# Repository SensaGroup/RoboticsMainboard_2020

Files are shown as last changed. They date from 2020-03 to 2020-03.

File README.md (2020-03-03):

# SENSA - Robotics_Mainboard

SENSA Mainboard is used on the Eurobot 2020 competition.

## Description
The Mainboard is the commander of the robot system. 
We used an Arduino Mega for the base and we developed the extension board

## Features
- 5V/5VA/12V inputs with protection
- 2 Sockets for stepper drivers, based on the A4988 pinout
- 6x servo pinouts with external 5V power supply
- 6x 12V pneumatic valve controller
- 5x 1AMP relays 
- AX-12 support
- 6x optoisolated 12V infrared sensor inputs
- 6x binary 5V sensor inputs
- NRF24L01
- I2C/UART pinouts

## Software
All software is written in C for AVR.
View README in the Software folder.

## Pictures
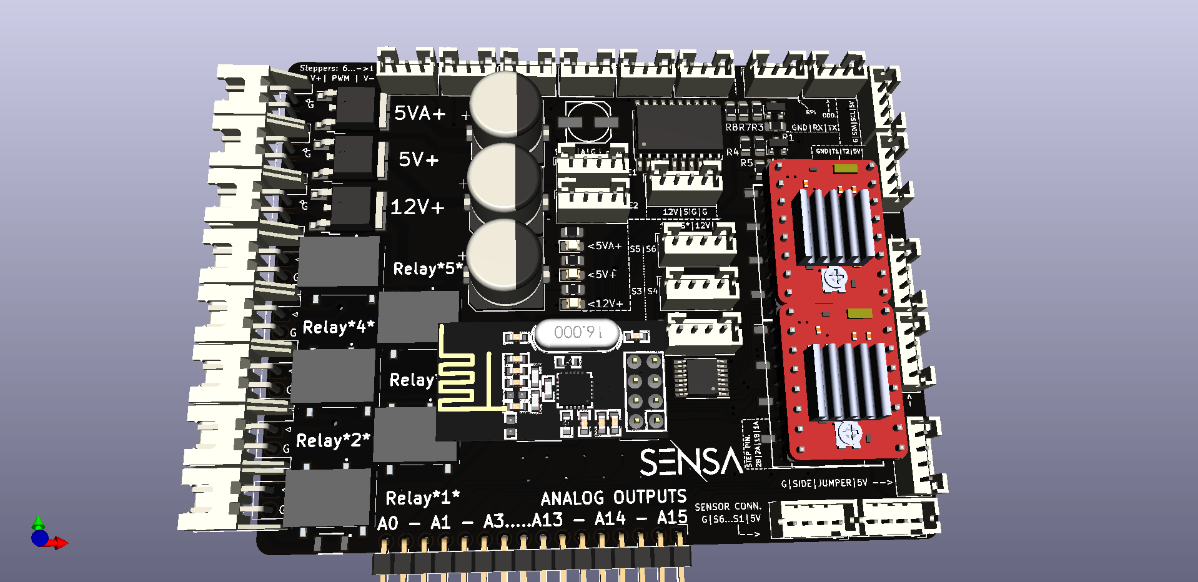
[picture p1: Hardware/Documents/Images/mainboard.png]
Top_view


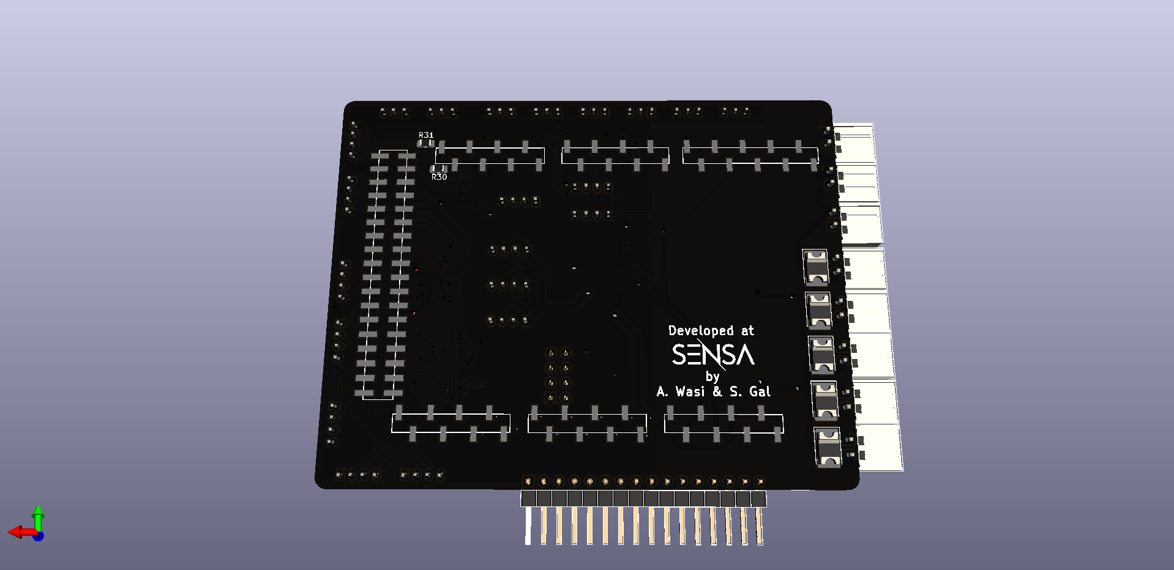
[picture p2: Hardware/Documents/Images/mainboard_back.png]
Back_view


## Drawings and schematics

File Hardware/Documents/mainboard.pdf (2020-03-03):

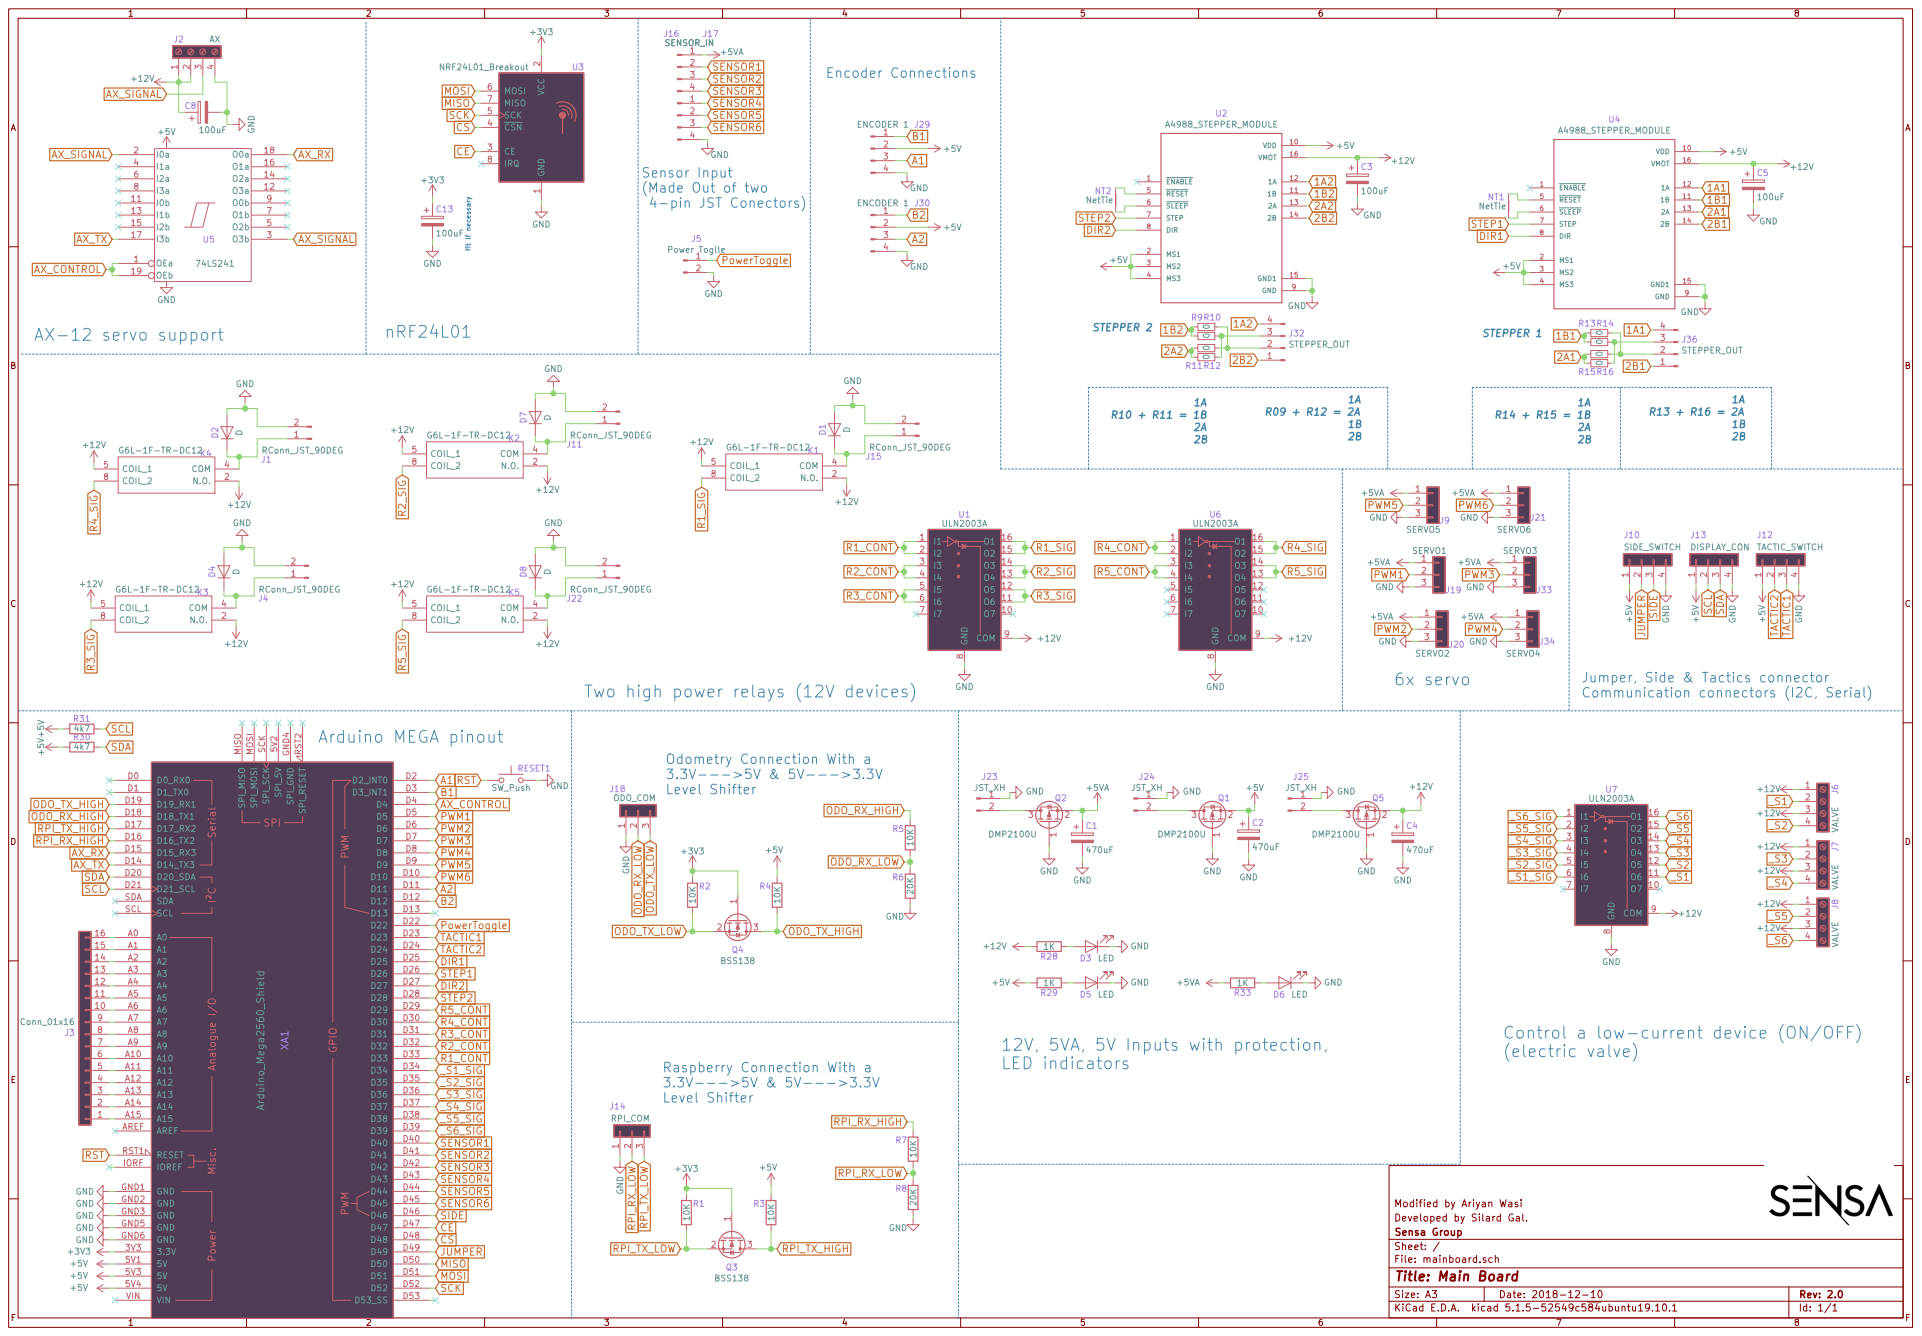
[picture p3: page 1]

2 CE 3 CSN 4 SCK 5 MOSI 6 MISO 7

2B Sensor Input
(Made Out of two
4-pin JST Conectors)

6x servo Two high power relays (12V devices)

Jumper, Side & Tactics connector
Communication connectors (I2C, Serial)

Control a low-current device (ON/OFF)
(electric valve)

Modified by Ariyan Wasi
Developed by Silard Gal.
File: mainboard.sch Sheet: / Sensa Group

Id: 1/1 Title: Main Board

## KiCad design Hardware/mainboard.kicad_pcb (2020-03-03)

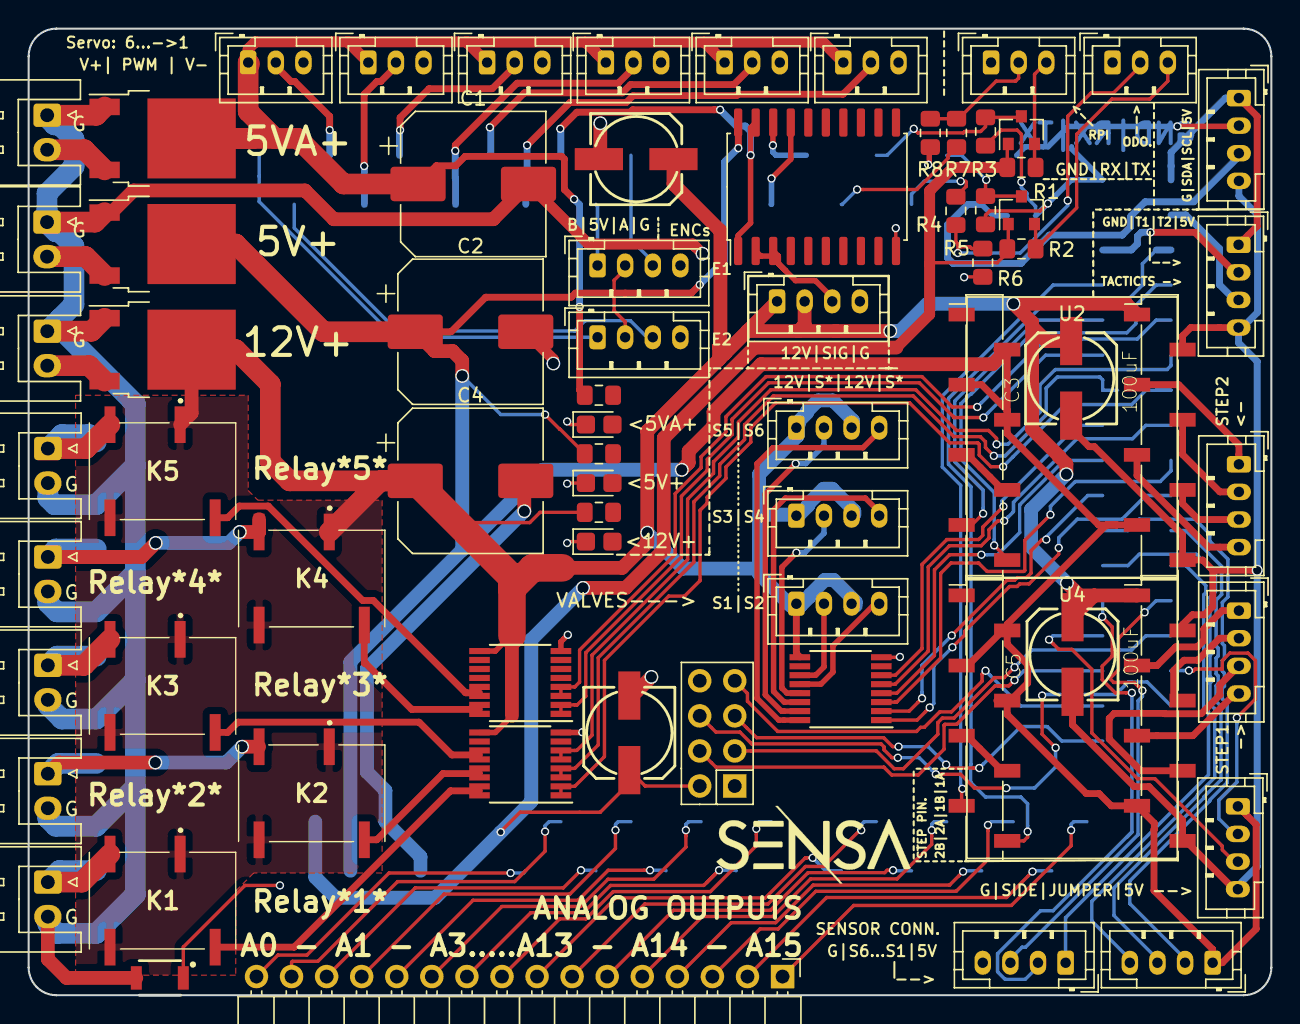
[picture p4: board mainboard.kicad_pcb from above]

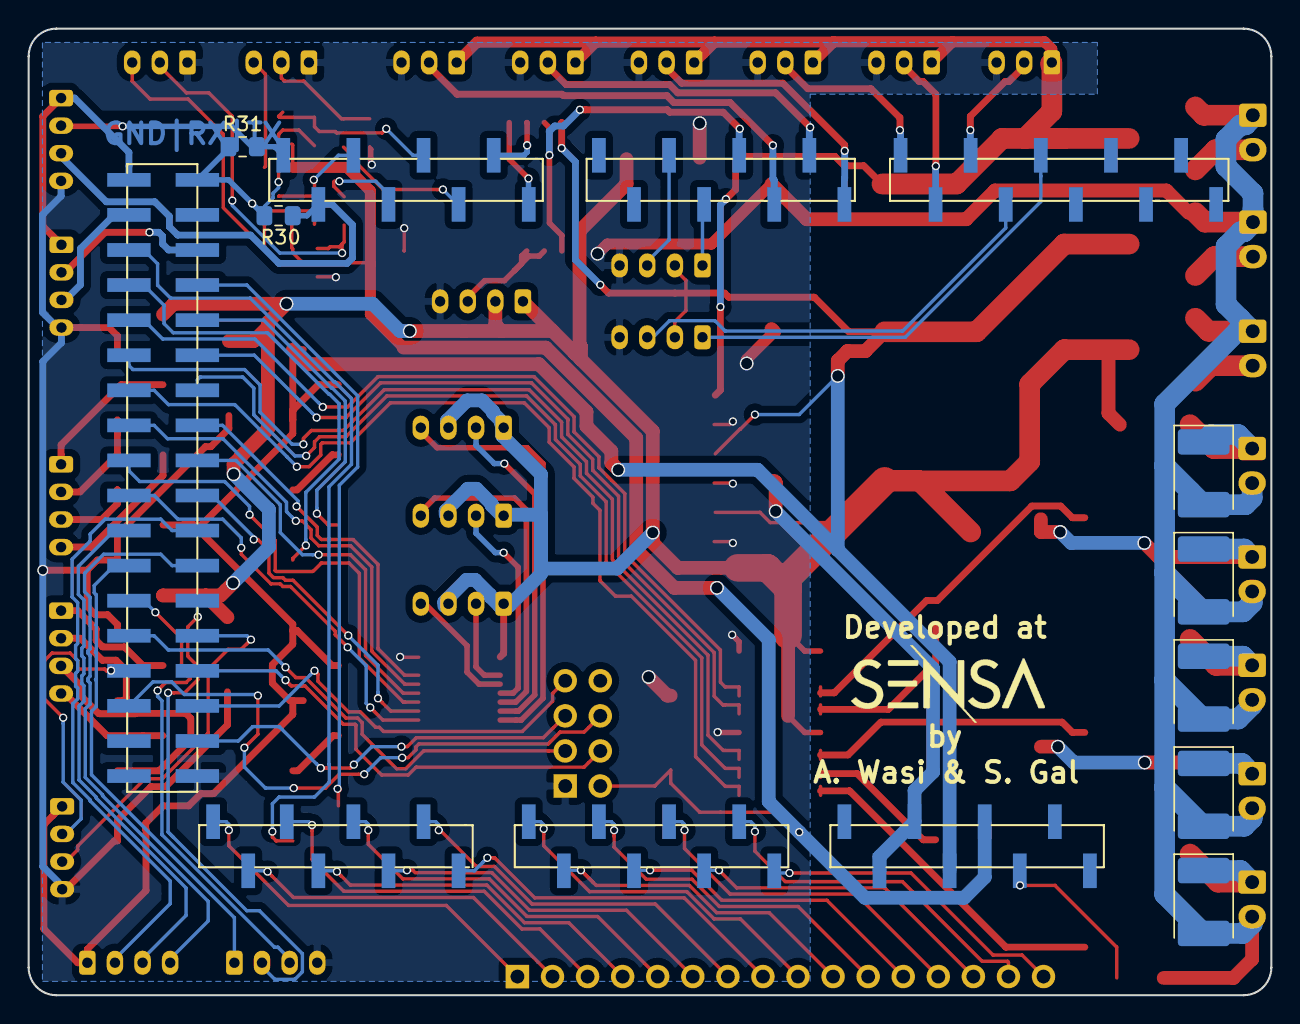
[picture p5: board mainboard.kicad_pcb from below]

Board: 2 copper layers, 90.0 x 70.0 mm, 79 parts (7 on the bottom side), 110 nets.

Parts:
5V+, 5VA+, 12V+: JST_XH; JST_XH_S2B-XH-A_1x02_P2.50mm_Horizontal
12V|S*|12V|S*: VALVE; JST_PH_B4B-PH-K_1x04_P2.00mm_Vertical
B|5V|A|G: ENCODER 1; JST_PH_B4B-PH-K_1x04_P2.00mm_Vertical
C1, C2, C4: 470uF; CP_Elec_10x10
C3, C5, C8, C13: 100uF; CAPAE0607X600N
D1, D2, D4, D7, D8: D; D_2114_3652Metric_Pad1.85x3.75mm_HandSolder
D3, D5, D6: LED; LED_0805_2012Metric_Castellated
G: RConn_JST_90DEG; JST_XH_S2B-XH-A_1x02_P2.50mm_Horizontal
G#2, G#3, G#4, G#5: RConn_JST_90DEG; JST_XH_S2B-XH-A_1x02_P2.50mm_Horizontal
J2: AX; JST_PH_B4B-PH-K_1x04_P2.00mm_Vertical
J3: Conn_01x16; PinHeader_1x16_P2.54mm_Horizontal
J7: VALVE; JST_PH_B4B-PH-K_1x04_P2.00mm_Vertical
J9: SERVO5; JST_PH_B3B-PH-K_1x03_P2.00mm_Vertical
J10: SIDE_SWITCH; JST_PH_B4B-PH-K_1x04_P2.00mm_Vertical
J12: TACTIC_SWITCH; JST_PH_B4B-PH-K_1x04_P2.00mm_Vertical
J13: DISPLAY_CON; JST_PH_B4B-PH-K_1x04_P2.00mm_Vertical
J14: RPI_COM; JST_PH_B3B-PH-K_1x03_P2.00mm_Vertical
J16, J17: SENSOR_IN; JST_PH_B4B-PH-K_1x04_P2.00mm_Vertical
J18: ODO_COM; JST_PH_B3B-PH-K_1x03_P2.00mm_Vertical
J19: SERVO1; JST_PH_B3B-PH-K_1x03_P2.00mm_Vertical
J20: SERVO2; JST_PH_B3B-PH-K_1x03_P2.00mm_Vertical
J21: SERVO6; JST_PH_B3B-PH-K_1x03_P2.00mm_Vertical
J30: ENCODER 1; JST_PH_B4B-PH-K_1x04_P2.00mm_Vertical
J32, J36: STEPPER_OUT; JST_PH_B4B-PH-K_1x04_P2.00mm_Vertical
J33: SERVO3; JST_PH_B3B-PH-K_1x03_P2.00mm_Vertical
J34: SERVO4; JST_PH_B3B-PH-K_1x03_P2.00mm_Vertical
K1, K2, K3, K4, K5: G6L-1F-TR-DC12; G6L1FTRDC5
NT1, NT2: NetTie; NetTie-2_SMD_Pad0.5mm
Q1, Q2, Q5: DMP2100U; TO-252-2
Q3, Q4: BSS138; SOT-23
R1, R2, R3, R4, R5, R7: 10K; R_0805_2012Metric_Pad1.15x1.40mm_HandSolder
R6, R8: 20K; R_0805_2012Metric_Pad1.15x1.40mm_HandSolder
R28, R29, R33: 1K; R_0805_2012Metric_Pad1.15x1.40mm_HandSolder
R30, R31: 4k7; R_0805_2012Metric_Pad1.15x1.40mm_HandSolder
RESET1: SW_Push; B3U-1000P
S1,S2: VALVE; JST_PH_B4B-PH-K_1x04_P2.00mm_Vertical
U1, U6, U7: ULN2003A; TSSOP-16_4.4x5mm_P0.65mm
U2, U4: A4988_STEPPER_MODULE; STEP_SMD
U3: NRF24L01_Breakout; PinSocket_2x04_P2.54mm_Vertical
U5: 74LS241; SOIC-20W_7.5x12.8mm_P1.27mm
XA1: Arduino_Mega2560_Shield

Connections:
1A1: J36.4, U4.12
1A2: J32.4, U2.12
1B1: J36.3, U4.11
1B2: J32.3, U2.11
2A1: J36.2, U4.13
2A2: J32.2, U2.13
2B1: J36.1, U4.14
2B2: J32.1, U2.14
+3V3: C13.+, Q3.1, Q4.1, R1.1, R2.1, U3.2, XA1.3V3
+5V: B|5V|A|G.2, C2.1, J10.1, J12.1, J13.1, J30.2, Q1.2, R3.1, R4.1, R29.2, R30.1, R31.1, U2.2, U2.3, U2.4, U2.10, U4.2, U4.3, U4.4, U4.10, U5.20, XA1.5V1, XA1.5V3, XA1.5V4
+5VA: C1.1, J9.1, J16.1, J19.1, J20.1, J21.1, J33.1, J34.1, Q2.2, R33.2
+12V: 12V|S*|12V|S*.1, 12V|S*|12V|S*.3, C3.+, C4.1, C5.+, C8.+, J2.1, J2.2, J7.1, J7.3, K1.2, K1.5, K2.2, K2.5, K3.2, K3.5, K4.2, K4.5, K5.2, K5.5, Q5.2, R28.2, S1,S2.1, S1,S2.3, U1.9, U2.16, U4.16, U6.9, U7.9
A1: B|5V|A|G.3, XA1.D2
A2: J30.3, XA1.D11
AX_CONTROL: U5.1, U5.19, XA1.D4
AX_RX: U5.18, XA1.D15
AX_SIGNAL: J2.3, U5.2, U5.3
AX_TX: U5.17, XA1.D14
B1: B|5V|A|G.1, XA1.D3
B2: J30.1, XA1.D12
CE: U3.3, XA1.D47
CS: U3.4, XA1.D48
DIR1: U4.8, XA1.D25
DIR2: U2.8, XA1.D27
GND: 5V+.1, 5VA+.1, 12V+.1, B|5V|A|G.4, C1.2, C2.2, C3.-, C4.2, C5.-, C8.-, C13.-, D1.2, D2.2, D3.1, D4.2, D5.1, D6.1, D7.2, D8.2, G.2, G#2.2, G#3.2, G#4.2, G#5.2, J2.4, J9.3, J10.4, J12.4, J13.4, J14.1, J17.4, J18.1, J19.3, J20.3, J21.3, J30.4, J33.3, J34.3, Q1.1, Q2.1, Q5.1, R6.2, R8.2, RESET1.2, U1.8, U2.9, U2.15, U3.1, U4.9, U4.15, U5.10, U6.8, U7.8, XA1.GND1, XA1.GND2, XA1.GND3, XA1.GND5, XA1.GND6
JUMPER: J10.2, XA1.D49
MISO: U3.7, XA1.D50
MOSI: U3.6, XA1.D51
unnamed: D1.1, G#4.1, K1.4
unnamed: D2.1, G.1, K4.4
unnamed: D3.2, R28.1
unnamed: D4.1, G#2.1, K3.4
unnamed: D5.2, R29.1
unnamed: D6.2, R33.1
unnamed: D7.1, G#3.1, K2.4
unnamed: D8.1, G#5.1, K5.4
unnamed: J3.1, XA1.A15
unnamed: J3.2, XA1.A14
unnamed: J3.3, XA1.A13
unnamed: J3.4, XA1.A12
unnamed: J3.5, XA1.A11
unnamed: J3.6, XA1.A10
unnamed: J3.7, XA1.A9
unnamed: J3.8, XA1.A8
unnamed: J3.9, XA1.A7
unnamed: J3.10, XA1.A6
unnamed: J3.11, XA1.A5
unnamed: J3.12, XA1.A4
unnamed: J3.13, XA1.A3
unnamed: J3.14, XA1.A2
unnamed: J3.15, XA1.A1
unnamed: J3.16, XA1.A0
unnamed: 5VA+.2, Q2.3
unnamed: 5V+.2, Q1.3
unnamed: 12V+.2, Q5.3
unnamed: NT1.1, U4.5
unnamed: NT1.2, U4.6
unnamed: NT2.1, U2.5
unnamed: NT2.2, U2.6
ODO_RX_HIGH: R5.1, XA1.D18
ODO_RX_LOW: J18.2, R5.2, R6.1
ODO_TX_HIGH: Q4.3, R4.2, XA1.D19
ODO_TX_LOW: J18.3, Q4.2, R2.2
PWM1: J19.2, XA1.D5
PWM2: J20.2, XA1.D6
PWM3: J33.2, XA1.D7
PWM4: J34.2, XA1.D8
PWM5: J9.2, XA1.D9
PWM6: J21.2, XA1.D10
R1_CONT: U1.1, U1.2, XA1.D33
R1_SIG: K1.8, U1.15, U1.16
R2_CONT: U1.3, U1.4, XA1.D32
R2_SIG: K2.8, U1.13, U1.14
R3_CONT: U1.5, U1.6, XA1.D31
R3_SIG: K3.8, U1.11, U1.12
R4_CONT: U6.1, U6.2, XA1.D30
R4_SIG: K4.8, U6.15, U6.16
R5_CONT: U6.3, U6.4, XA1.D29
R5_SIG: K5.8, U6.13, U6.14
RPI_RX_HIGH: R7.1, XA1.D16
RPI_RX_LOW: J14.2, R7.2, R8.1
RPI_TX_HIGH: Q3.3, R3.2, XA1.D17
RPI_TX_LOW: J14.3, Q3.2, R1.2
RST: RESET1.1, XA1.RST1
SCK: U3.5, XA1.D52
SCL: J13.2, R31.2, XA1.D21
SDA: J13.3, R30.2, XA1.D20
SENSOR1: J16.2, XA1.D40
SENSOR2: J16.3, XA1.D41
SENSOR3: J16.4, XA1.D42
SENSOR4: J17.1, XA1.D43
SENSOR5: J17.2, XA1.D44
SENSOR6: J17.3, XA1.D45
SIDE: J10.3, XA1.D46
STEP1: U4.7, XA1.D26
STEP2: U2.7, XA1.D28
TACTIC1: J12.3, XA1.D23
TACTIC2: J12.2, XA1.D24
_S1: S1,S2.2, U7.11
_S1_SIG: U7.6, XA1.D34
_S2: S1,S2.4, U7.12
_S2_SIG: U7.5, XA1.D35
_S3: J7.2, U7.13
_S3_SIG: U7.4, XA1.D36
_S4: J7.4, U7.14
_S4_SIG: U7.3, XA1.D37
_S5: 12V|S*|12V|S*.2, U7.15
_S5_SIG: U7.2, XA1.D38
_S6: 12V|S*|12V|S*.4, U7.16
_S6_SIG: U7.1, XA1.D39

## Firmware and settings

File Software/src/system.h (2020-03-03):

#ifndef SYSTEM_H
#define SYSTEM_H

#include <Arduino.h>
#include "actuator.h"
#include "TimerThree.h" 
#include "nrf.h"
#include "can.h"
#include "odometry.h"
#include "mechanism.h"
#include "detection.h"

#define PIN_JUMPER  3
#define PIN_TACTIC1 5
#define PIN_TACTIC2 6
#define PIN_SIDE    4

void init_system(void);
void set_match_started(void);
unsigned long get_sys_time(void);

int get_tactic1(void);
int get_tactic2(void);
int get_side(void);

struct goto_fields
{
	struct odometry_position goto_position;
	uint8_t speed;
	uint8_t direction;
	uint8_t	(*callback)();
	uint8_t (*callback_end)();
};


#endif
